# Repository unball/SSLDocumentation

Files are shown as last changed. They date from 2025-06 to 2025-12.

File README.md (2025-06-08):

# SSLDocumentation
Documentação do SSL (Small Size League) da Equipe UnBall

## Indice

- [Fundamentação Teórica](./FundamentacaoTeorica/README.md)
- [Elétrica](./Hardware/Eletrica/README.md)
    - [Componentes](./Hardware/Eletrica/Componentes/README.md)
    - [Movimentação](./Hardware/Eletrica/Projeto-Movimentacao/README.md)
    - [Chute](./Hardware/Eletrica/Projeto-Chute/README.md)
- [Mecânica](./Hardware/Mecanica/README.md)
    - [Base](./Hardware/Mecanica/Base/README.md)
    - [Camisa](./Hardware/Mecanica/Camisa/README.md)
    - [Chute](./Hardware/Mecanica/Chute/README.md)
- [Infraestrutura para testes](./Hardware/Infraestrutura/README.md)
    - [Campo](./Hardware/Infraestrutura/Campo/README.md)
    - [Gol](./Hardware/Infraestrutura/Gol/README.md)
    - [Visão](./Hardware/Infraestrutura/Visao/README.md)
    - [Bancada de Testes](./Hardware/Infraestrutura/BancadaTestes/README.md)
- [Software do Robô](./Software/Robo/README.md)
    - [Firmware](./Software/Robo/Firmware.md)
- [Software da Estratégia](./Software/Estrategia/)
    - [Client](./Software/Estrategia/Client/README.md)
    - [Navegação](./Software/Estrategia/Navegacao/README.md)
    - [Decisão](./Software/Estrategia/Decisao/README.md)

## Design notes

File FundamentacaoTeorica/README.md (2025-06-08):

# Fundamentação Teórica

1. [Design do sistema](Design-sistema.md)
2. [Design do robô](Design-robo.md)
    - [Motor](./Motor/Motor.md)
    - [Acionamento do motor](./Motor/Acionamento-Motor.md)
    - [Rodas](./Rodas/Estudo-tipo-rodas.md)
    - [Cinemática](./Cinematica/Cinematica-robo.md)
    - [Comunicação](./Comunicacao/Comunicacao.md)

## A incluir:
- Sistema de chute

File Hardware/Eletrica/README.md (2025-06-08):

# Sistema elétrico

## Protótipo movimentação

O protótipo será feito por fabricação manual de PCBs em placa de cobre

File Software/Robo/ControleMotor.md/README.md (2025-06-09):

# Controle do motor

## Primeiro passo: controle do torque

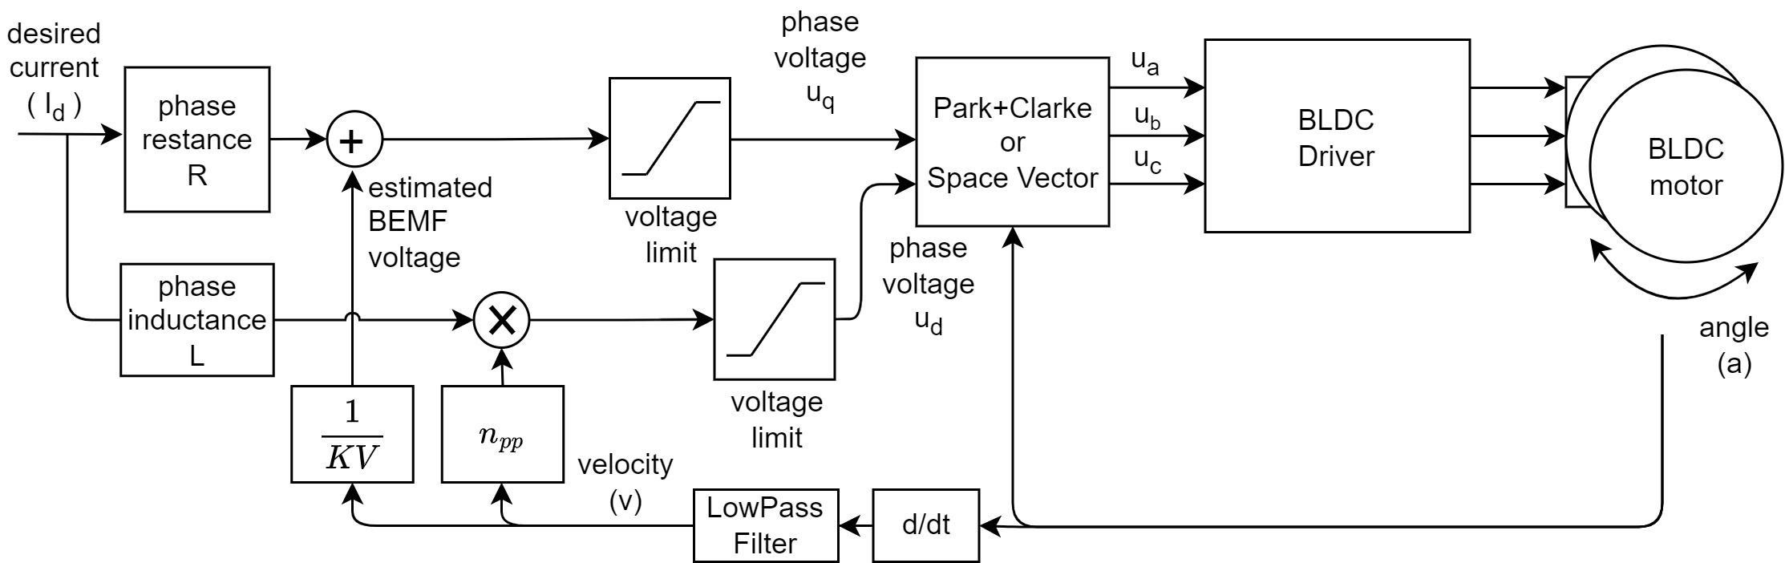
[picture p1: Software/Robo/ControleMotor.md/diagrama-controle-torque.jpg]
Controle-Torque

https://docs.simplefoc.com/voltage_torque_mode
Precisa encontrar os seguintes valores: https://docs.simplefoc.com/bldcmotor

- numero de polos do motor

- indutância L

- KV

- phase resistance 

https://github.com/makerbase-motor/MKS-ESP32FOC/blob/MKS-ESP32-FOC-V1.0/Test%20Code/7_current_control_example/7_current_control_example.ino

https://docs.arduino.cc/software/ide-v2/tutorials/ide-v2-serial-plotter/

https://docs.simplefoc.com/code

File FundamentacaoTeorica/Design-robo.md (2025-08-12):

# Design do robô

## Limitações no design advindas das regras do SSL

### Tamanho 

- O robô deve caber dentro de um cilindro com 0.18m de largura e 0.15m de altura 

### Cores do casco 

- As cores devem ser as mesmas para todos os robôs sendo em um esquema de cor clara e cor escura 
- A cor deve cobrir ao menos 6cm da altura máxima do robô 
- O casco não pode ser refletivo para não interferir na visão 
- As cores não podem ser próximas das cores usadas nos padrões da visão e bola 
- As cores não podem sair durante os jogos 

### Ações do robô 

- O robô deve se movimentar no campo, respondendo aos eventos 
- Para participarmos de competições mundiais, o robô deve chutar a bola 

## Design robô SSL - UnBall

Para facilitar o desenvolvimento do robô, foram definidas etapas para elaborar cada ação que o robô deve fazer no campo quando receber as ações da Estratégia:

### Sistema de Movimentação do Robô

Diz respeito a como o robô vai se movimentar no campo. Para isso, precisamos definir:

- Qual motor usar e como acionar com velocidade desejada?
    - [Estudo do motor](./Motor/Motor.md)
    - [Estudo de como acionar o motor](./Motor/Acionamento-Motor.md)
- Qual roda usar?
    - [Estudo de rodas para robôs omnidirecionais](./Rodas/Estudo-tipo-rodas.md)
- Como transformar a velocidade das rodas na velocidade do robô?
    - [Levantamento da cinemática do robô](./Cinematica/Cinematica-robo.md)
- Como o robô vai saber o que deve fazer?
    - [Comunicação do robô com a Estratégia](./Comunicacao/Comunicacao.md)

### Sistema de Chute

<!-- TODO: incluir links para o sistema de chute -->
Diz respeito a funcionalidade do robô de poder "chutar" a bola. Para isso, precisamos definir:

- Mecânica
- Sistema elétrico
- Quando o chute vai atuar?

## Referência

Buscamos responder as seguintes perguntas do livro _Introduction to autonomous robots_: 

- Como ele se move?
    > R.: Ele pode ir para todas as direções.

- Onde o robô irá se locomover?
    > R.: Em um carpete que será posicionado em cima de uma superfície plana. As dimensões do carpete segue as regras da categoria SSL 

- Como a velocidade das rodas afeta sua posição e velocidade no mundo?  
    > R.: Aqui definimos a cinemática do robô. Isso é detalhado no arquivo [Cinemática](./Cinematica/Cinematica-robo.md)

- Como podemos controlar a velocidade das rodas para atingir uma determinada posição? 
    > R.: Aqui definimos a forma como vai funcionar a Navegação do Robô. Isso é feito na Estratégia. Os detalhes da Estratégia como qual método de navegação vamos usar e qual sistema de decisão vamos aplicar pode ser visto em [Navegação](./Estrategia/Navegacao.md) e [Decisão](./Estrategia/Decisao.md), respectivamente.

- Quais sensores o robô usará pra perceber seu próprio estado no mundo? 
    > R.: As câmeras posicionadas acima do campo dirão sua posição. O giroscópio mede sua orientação em relação ao proprio eixo e o sensor infravermelho irá confirmar se a bola está perto do robô ou não 

- Como extrair informações de seus sensores?
    > R.: Através do Sistema de Visão Computacional Unificado gerido pela organização da categoria SSL. 

- Como o erro da sua percepção no mundo pode ser representado e como lidar diante de situações incertas? 
    > R.: Isso vai ser detalhado em [Navegação](./Estrategia/Navegacao.md) e [Decisão](./Estrategia/Decisao.md).

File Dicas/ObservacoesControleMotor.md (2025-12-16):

# Comentários a respeito do projeto do Controle do Motor GM4108120T com MKS ESP32 DUAL FOC V1.0

## Sobre o driver

### Desvantagens

Não consegue lidar bem com pico de corrente.

Não suporta execução sem limite de corrente.

Sensor de corrente é horrível.

Esp32 ser embutida só trouxe prejuízo. Fica muito dificil de corrigir em hardware os problemas com o sensor de corrente.

Não consegue lidar bem aplicando carga no motor.

Não consegue lidar bem com mau contato no encoder. 

O fusível de proteção queima porém outro componente também queima junto. Não parecia proteger nada.

## Sobre o motor

### Vantagens

É uma opção mais barata que até onde foi usada, se mostrou suficiente.

### Desvantagens

Fabricante chinesa não fornece todas as especificações importantes pro controle do motor. Muitos parâmetros foram assumidos.

O motor sem encoder, vem sem o ímã direcional no eixo.

## Sobre SimpleFOC

### Vantagens

A abstração do FOC em código realmente ajudou a entender melhor como controlar o motor BLDC. 
Seguindo a documentação, é fácil de configurar para usar com o MKS ESP32 DUAL FOC V1.0

### Desvantagens

O uso de tecnicas pra melhorar o controle pode ficar bem engessado pela biblioteca. Se quiser incluir um filtro passa-baixas ou implementar outro controlador, tem que mexer no código fonte da biblioteca

A biblioteca assume que a frequência do loop() do microcontrolador é suficiente pra considerar a discretização do controle como algo contínuo e dá pra sentir como assumir isso deu problemas na prática. Se fosse outra aplicação, menos focada na velocidade do motor, talvez assumir isso não tenha tanto impacto.

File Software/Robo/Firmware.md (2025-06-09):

# Firmware

Arquitetura 

Legenda 

Sistema Central 

Onde fica a inteligência do robô. Vai receber a velocidade (em rad/s ou rpm, depende do que o controle decidir) que o robô deve ter naquele momento e repassar a velocidade para os motores. Também vai receber quando o robô deve fazer o chute 

Comunicação entre microcontroladores 

A comunicação é feita por fio, utilizando o protocolo I2C 

Sistema Periférico 

Não é a parte inteligente mas realiza os cálculos necessários para transformar a velocidade recebida do computador em tensão para as fases do motor. Como o motor é BLDC, precisa de um algoritmo de controle de rotação mais complexo que apenas mandar a tensão para o motor. Para que a rotação seja mais precisa, utilizamos a leitura do encoder que está no motor. 

Comunicação entre driver e motores 

É apenas um fio que envia a tensão de cada fase do motor para que ele gire corretamente 

Motores 

São os motores BDLC. Neles estão acoplados os encoders, que enviam a leitura da posição angular do motor para o Periférico 

Encoders 

São os fios de alimentação do encoder e também de transferência dos dados lidos para o Periférico 

Comentários: 

No diagrama é possível ver que há dois sistemas: 1) Central e 2) Periférico.  

No Sistema Central, temos uma ESP32 WROOM.  
 
No Sistema Periférico, também usamos ESP32 WROOM embutidas no driver MKS DUAL FOC v2.0.  

Cada driver comporta uma ESP e dois motores. Assim é possível executar o FOC o mais rápido possível sem que seus custos computacionais prejudique o acionamento do motor. Pelo menos essa é a ideia inicial.  

Implementação 

Arduíno & C++ 

Organização do código 

https://github.com/unball/FirmwarePerifericoSSL  

https://github.com/unball/FirmwareCentralSSL  

## Comunicação

PC -> roteador -> firmware central -> firmware periferico 

# Visão

# Estratégia

https://github.com/makerbase-motor/MKS-ESP32FOC/blob/MKS-ESP32-FOC-V2.0/Test%20Code/Read%20Before%20You%20Begin.txt 
    ② The open-loop control mode is a test routine, and the heating of the motor is inevitable. Be careful not to get burned!
Please do not run the open-loop routine for more than one minute, otherwise it will cause overheating and burn the motor or circuit board!

https://randomnerdtutorials.com/esp32-spi-communication-arduino/#multiple-devices-same-bus

https://www.quora.com/How-do-I-exchange-data-between-Arduino-and-ESP32-using-serial-communication

https://randomnerdtutorials.com/esp-now-two-way-communication-esp32/

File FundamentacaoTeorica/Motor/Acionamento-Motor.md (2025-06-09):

# Acionamento do motor

## Motor BDLC

### FOC

- [What is FOC? (Field Oriented Control) And why you should use it! || BLDC Motor](https://www.youtube.com/watch?v=Nhy6g9wGHow)
- [Field-Oriented Control](https://www.youtube.com/watch?v=_6-_jvZe7iA)
- [Field-Oriented Control - MathWorks](https://www.mathworks.com/discovery/field-oriented-control.html)

## Controle da velocidade do motor

- FOC
    - Precisa saber a posição do rotor
    - Precisa também monitorar a corrente para não ter perda de energia

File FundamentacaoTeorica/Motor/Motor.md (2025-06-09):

# Motor

## Como motor BDLC funciona

Explicações em Inglês:

- [Playlist Understanding Motors](https://www.youtube.com/watch?v=EHYEQM1sA3o&list=PLaBr_WzeIAixidGwqfcrQlwKZX4RZ2E7D&index=1)
> Explica conceitos mais básicos de eletromagnetismo até como motor BLDC funciona e alguns conceitos importantes para entender FOC

- [Brushless Motor - How they work BLDC ESC PWM](https://www.youtube.com/watch?v=yiD5nCfmbV0)
> Possui animações muito boas para entender como funciona a comutação em um motor BLDC

### Mais referências

- Explicação de como motores elétricos funcionam, com animações: [Playlist de The Engineering Mindset](https://www.youtube.com/watch?v=yiD5nCfmbV0&list=PLWv9VM947MKh3sZh5rjYxrrNno1Mc6cuu)

- Vídeos do MATLAB:
    - [https://www.youtube.com/watch?v=gNpoTPzEkco&t=81s](https://www.youtube.com/watch?v=gNpoTPzEkco&t=81s) 
    - [Understanding Six-step Commutation for BLDC motors| Brushless Motor Control with Simulink, Part 2](https://www.youtube.com/watch?v=WYJWdMV3YMs&t=1s)
    - [BLDC Speed Control Using Pulse Width Modulation (PWM)| Brushless Motor Control with Simulink, Part 3](https://www.youtube.com/watch?v=b5J5qkR7msc)
    - [Understanding Field-Oriented Control | Motor Control, Part 4](https://www.youtube.com/watch?v=YPD1_rcXBIE)
    - [Understanding Space Vector Modulation| Brushless Motor Control with Simulink, Part 5](https://www.youtube.com/watch?v=Gj7qAlsq_m8)
    - [10 Practical Considerations for Implementing Field-Oriented Control (FOC) | Brushless Motor Control](https://www.youtube.com/watch?v=ilN-DauXVFM)

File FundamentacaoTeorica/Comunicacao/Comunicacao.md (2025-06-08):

# Comunicação

## Wireless

### Quais opções temos? Por que vamos usar WiFi?

### WiFi

## Serial

### I2C

### SPI

### PWM

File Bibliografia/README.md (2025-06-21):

# Referências bibliográficas

## Robocup Small Size League Soccer

- [Rules](https://ssl.robocup.org/rules/)
- [Team description papers - TDP](https://ssl.robocup.org/team-description-papers/)
    > "The Team Description Papers (TDPs) and especially the Extended Team Description Papers (ETDPs) are a key element of research and advancement in the Small Size League. Every team is required to submit a TDP or ETDP when qualifying for the RoboCup, describing new concepts and ideas as well as valuable learning experiences."
    >
    > "To search through all TDPs, you can use the [RoboTeam Twente TDP Search Engine](https://tdpsearch.com/)"
- [Open source contributions](https://ssl.robocup.org/open-source-contributions/)
- [Technical Overview of the Small Size League](https://ssl.robocup.org/technical-overview-of-the-small-size-league/#ssl-components):

    SSL Components

## Modern Robotics - Online Course 

- [Playlist no Youtube](https://www.youtube.com/playlist?list=PLggLP4f-rq02vX0OQQ5vrCxbJrzamYDfx)
- [Página principal sobre os cursos online](https://hades.mech.northwestern.edu/index.php/Modern_Robotics#Online_Courses)
- [Códigos no Github](https://github.com/NxRLab/ModernRobotics)

## Documentação ROS 2

- [Cinemática de robôs móveis](https://control.ros.org/humble/doc/ros2_controllers/doc/mobile_robot_kinematics.html)

## Cinemática de robô movél

- [Omnidirectional Control - Raul Rojas](./artigos/omnidrive.pdf)
    > Encontrado na wiki do [RoboTeam Twente](https://wiki.roboteamtwente.nl/technical/control/start)

# Pontos interessantes de outros times 

> Foram escolhidos alguns pontos dos projetos open source de outros times como inspiração para nosso projeto 

## TIGERs-Mannheim

### Base do robô
- https://github.com/TIGERs-Mannheim/mechanics/blob/master/v2020/PDF/01_Grundplatte.pdf
- https://github.com/TIGERs-Mannheim/mechanics/blob/master/v2020/PDF/02_Mittelplatte.pdf
- https://github.com/TIGERs-Mannheim/mechanics/blob/master/v2020/PDF/03_Oberplatte.pdf 

### Chute
- https://github.com/TIGERs-Mannheim/mechanics/blob/master/v2020/PDF/30_Kicker%20Eisen.pdf
- https://github.com/TIGERs-Mannheim/mechanics/blob/master/v2020/PDF/31_Kicker%20Sichel.pdf
- https://github.com/TIGERs-Mannheim/mechanics/blob/master/v2020/PDF/32_Kicker%20Chip.pdf 

### Camisa

- https://github.com/TIGERs-Mannheim/mechanics/blob/master/v2020/STL/Robot/Geh%C3%A4use%20Unterplatte.stl 
- https://github.com/TIGERs-Mannheim/mechanics/blob/master/v2020/STL/Robot/Geh%C3%A4use%20Mantel.stl 

## RobotTeamTwente

### Mecânica
- https://github.com/RoboTeamTwente/mechanics/tree/main/v2024/STL 
- https://github.com/RoboTeamTwente/mechanics/tree/main/v2024/PDF

## RobotJackets

### Firmware
- https://github.com/RoboJackets/robocup-firmware/tree/master/doc 

- kicker -> https://github.com/RoboJackets/robocup-firmware/blob/master/doc/Kicker.md e aqui tbm:  https://github.com/RoboJackets/robocup-firmware/blob/master/doc/Firmware.md

## ZJUNlict

### Mecânica

- https://github.com/ZJUNlict/Mechanics

## Imortals

### Mecânica

- https://github.com/Ma-Ghasemieh/Immortals_ssl_opensource_mech

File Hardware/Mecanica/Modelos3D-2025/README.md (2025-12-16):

# Modelos 

Peças desenvolvidas para o protótipo em dezembro/2025

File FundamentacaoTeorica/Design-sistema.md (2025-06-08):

# Design do sistema 

<!-- TODO: incluir link para o material das equipes  -->
O sistema é desenvolvido seguindo as regras da categoria [Robocup Small Size League](https://robocup-ssl.github.io/ssl-rules/sslrules.pdf ). Além do que foi feito por outras equipes que participam da categoria há mais tempo tais como Tigers, Robocin, ITA, entre outras.

Diante desse cenário, temos que o sistema pode ser representado da seguinte forma:

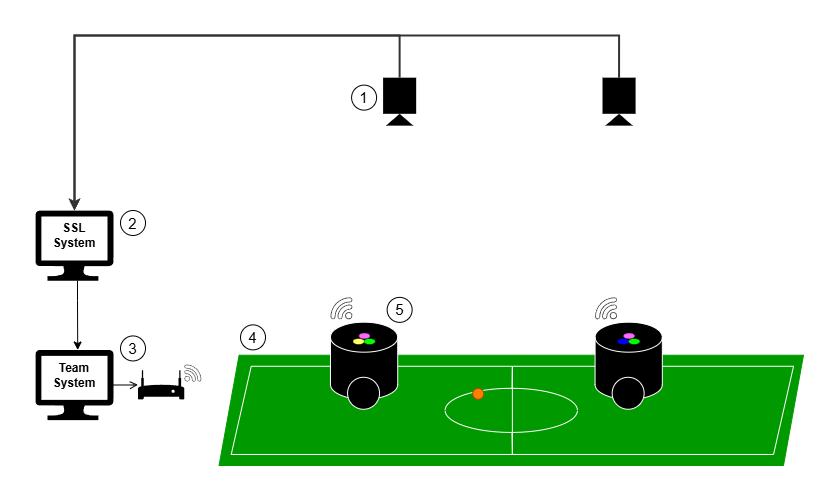
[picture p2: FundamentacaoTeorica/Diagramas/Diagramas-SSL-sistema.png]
Desenho simplificado do sistema do Small Size League


O sistema conta com:

<!-- TODO: incluir quais cameras sao geralmente usadas -->
1 - Sistema de Visão

- Duas câmeras posicionadas acima do campo
- Software de visão computacional unificado, que processa as informações lidas pelas câmeras e envia para os Sistemas de Software das equipes

<!-- TODO: incluir referencia para os repositorios do SSL -->
2 - Sistema SSL

- Consiste do Software de Visão Computacional e do Game Controller

<!-- TODO: incluir link para os softwares da equipe -->
3 - Sistema de software da Equipe

- Recebe as informações processadas pelo Sistema de Visão. No caso da Equipe UnBall, ao receber as informações, processa a navegação e decide a ação de cada robô do time naquele momento. A decisão é enviada, então, para cada robô via comunicação wireless. No desenho, essa comunicação se dá por WiFi, mas pode ser de outros tipos desde que atenda às regras da categoria.

4 - Campo

- O campo é feito de carpete e segue as regras definidas pela Robocup. 
- A bola é uma bola de golfe laranja
- Os gols, que não foram desenhados no diagrama acima, devem ser brancos e de dimensões de acordo com as regras da categoria.

5 - Robôs

- Os robôs compõe o time e, de acordo com as regras, possuem restrições em tamanho de 18cm de diâmetro e 15cm de altura. Eles recebem as ações decididas pelo Sistema da Equipe e atuam para tal. Além de se movimentar para o local decidido, eles podem chutar e driblar. Os robôs da UnBall apenas movimentam e chutam com força máxima.

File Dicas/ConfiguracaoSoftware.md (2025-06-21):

# Tutoriais de instalação dos softwares usados no SSL

## Requisitos mínimos para executar os sistemas de software
[A definir]

----

> :information_source: Info :information_source::
>
> Para saber mais sobre os softwares, acessar [Technical Overview of the Small Size League](https://ssl.robocup.org/technical-overview-of-the-small-size-league/)

1. [Tutorial SSL-Vision](https://github.com/unball/tutoriaisunballmd/blob/main/tutorialsslvision.md)

2. [Tutorial GrSim](https://github.com/unball/tutoriaisunballmd/blob/main/GrSim.md)

3. [SSL Game Controller](https://github.com/RoboCup-SSL/ssl-game-controller)

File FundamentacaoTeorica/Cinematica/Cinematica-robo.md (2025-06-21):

# Cinemática

<!-- TODO: o que é a cinematica e por que vamos precisar dela?  -->

## Definir configuração das rodas do robô

### Possíveis configurações do robô omnidirecional 
 
Vamos trabalhar com robôs holonomicos: Não tem restrição de movimento. Ele pode ir para qualquer lugar a qualquer instante. Pode ter 3 rodas ou 4 rodas 

#### Configuração do robô com 3 rodas

Três rodas omni montadas em uma configuração triangular com seus eixos inclinado em 120 graus em relação entre si:

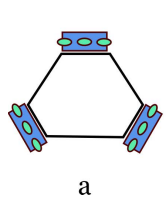
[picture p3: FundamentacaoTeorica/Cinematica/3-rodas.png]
3-rodas


#### Configuração do robô com 4 rodas

Rodas omni simétricas em 90 graus. Configuração '+' em b e 'x' em c:

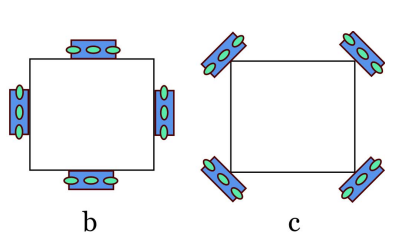
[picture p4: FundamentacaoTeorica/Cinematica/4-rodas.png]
dois tipos de omni com 4 rodas


Rodas mecanum como se fosse um carro:

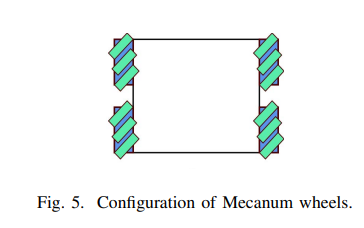
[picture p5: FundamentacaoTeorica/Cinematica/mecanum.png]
carro


#### Comparação entre 3 rodas e 4 rodas em 'x' 
> Referência: Modeling and Assessing of omni-directional robots with three and four wheels 

|  | Número de rodas | Tipo de rodas | Prós pro SSL | Contras pro SSL |
|---|---|---|---|---|
| Omni | 3 | Omni | Cria 3 pontos de contato (um plano) com mesma pressão nas rodas. Precisa de menor corrente pra atingir velocidade máxima que 4 rodas | Aceleração menor que 4 rodas |
| Omni | 4 | Omni | Aceleração bem mais rápida | Consome mais potência. Pode precisar de suspensão pra compensar a roda que fica suspensa e garantir pressão igual nas rodas que ficam no chão |
| "Carro" | 4 | Mecanum |  | Pode não caber bem dentro do cilindro limite da categoria. Qualquer espaço é sagrado |

*Observação:* 

É possível usar rodas mecanum em robôs omni na configuração de 3 rodas e 4 rodas. Porém a roda mecanum pode gerar uma limitação na movimentação do robô que deve ser considerada no projeto do controle do robô. Também não foram encontrados exemplos usando algo assim, então pra ter certeza que funcionaria no SSL teria que fazer algum estudo primeiro.  

### Configuração escolhida e justificativa 

#### Configuração de 4 rodas omnidirecionais

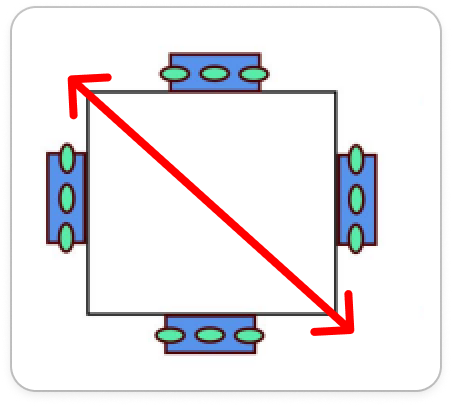
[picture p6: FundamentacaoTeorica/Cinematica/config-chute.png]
4 rodas omni


##### Motivos: 

1. Tem espaço pro sistema de chute, como indicado na figura pela seta vermelha 
2. Permite "esconder" as rodas com a camisa do robô  
3. Aceleração maior com 4 rodas indica que robô vai ser mais rápido para chegar na bola, pra defender a área aliada, etc 

## Formulação matemática

<!-- TODO: incluir formulas da cinematica do robo  -->

> Referência: [Omnidirectional Control](../../Bibliografia/artigos/omnidrive.pdf)

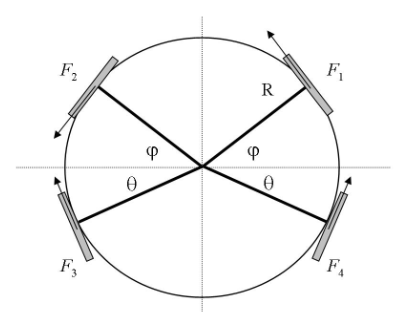
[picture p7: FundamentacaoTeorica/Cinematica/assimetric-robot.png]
Robô assimétrico


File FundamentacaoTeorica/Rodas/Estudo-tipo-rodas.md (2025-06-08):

# Tipos de rodas para robôs omnidirecionais 

## Comparação entre os tipos de rodas: 
> Fonte: A Comparative Review of Omnidirectional Wheel Types for Mobile Robotics 

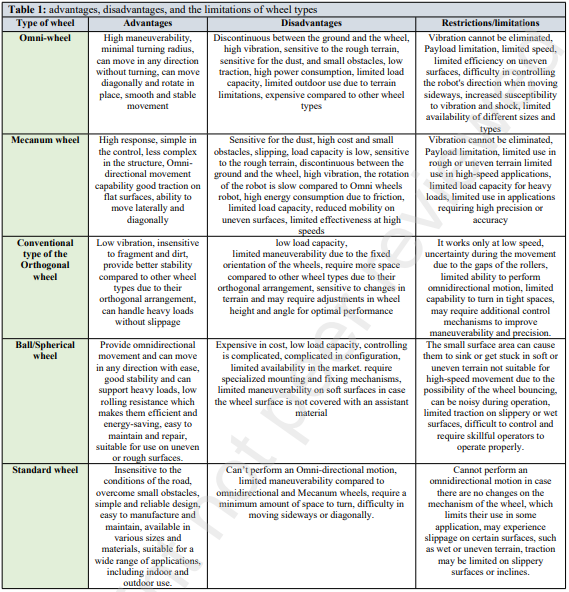
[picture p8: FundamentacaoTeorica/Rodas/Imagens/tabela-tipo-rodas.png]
tabela com tipos de rodas para robôs omnidirecionais

 
### Roda omnidirecional 
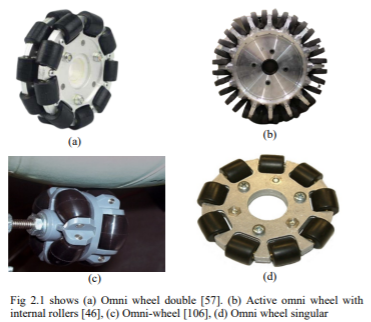
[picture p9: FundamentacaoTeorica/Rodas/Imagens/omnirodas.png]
roda omnidirecional


### Roda mecanum
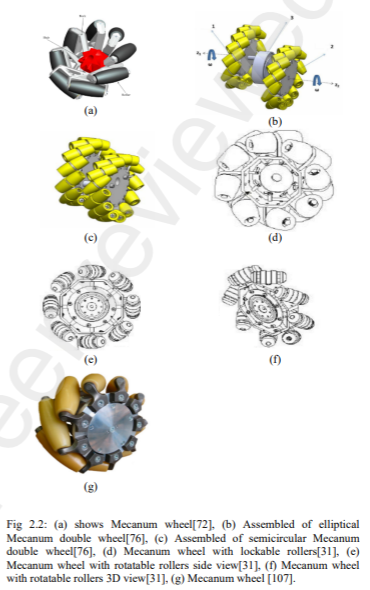
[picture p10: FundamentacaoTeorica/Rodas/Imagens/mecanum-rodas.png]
roda mecanum


### Roda ortogonal 
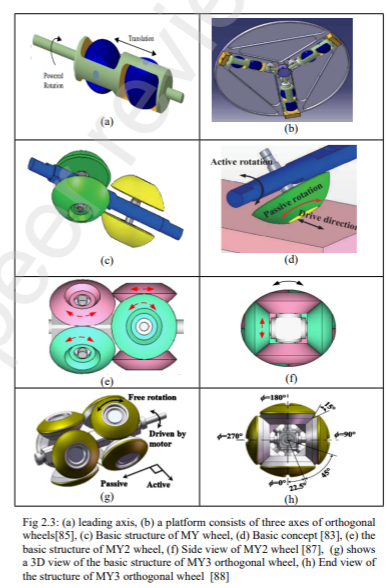
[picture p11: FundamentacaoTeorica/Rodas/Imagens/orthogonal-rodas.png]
roda ortogonal


### Roda esférica  
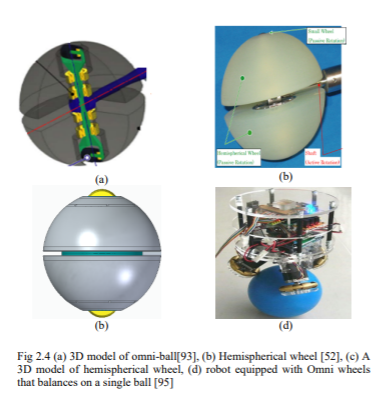
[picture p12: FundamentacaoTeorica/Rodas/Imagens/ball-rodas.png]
roda esferica


### Roda tradicional 
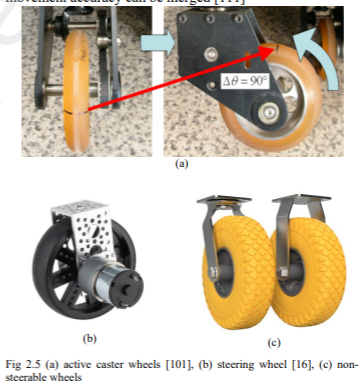
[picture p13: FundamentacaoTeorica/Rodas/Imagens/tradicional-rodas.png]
roda tradicional


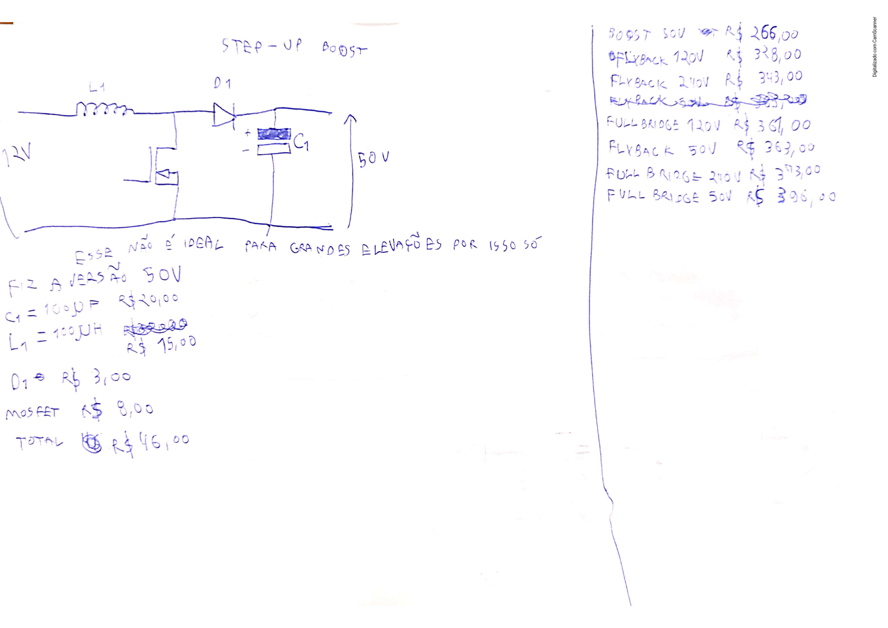
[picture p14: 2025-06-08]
Hardware/Eletrica/Projeto-Chute/Imagens/GetImage (11).png

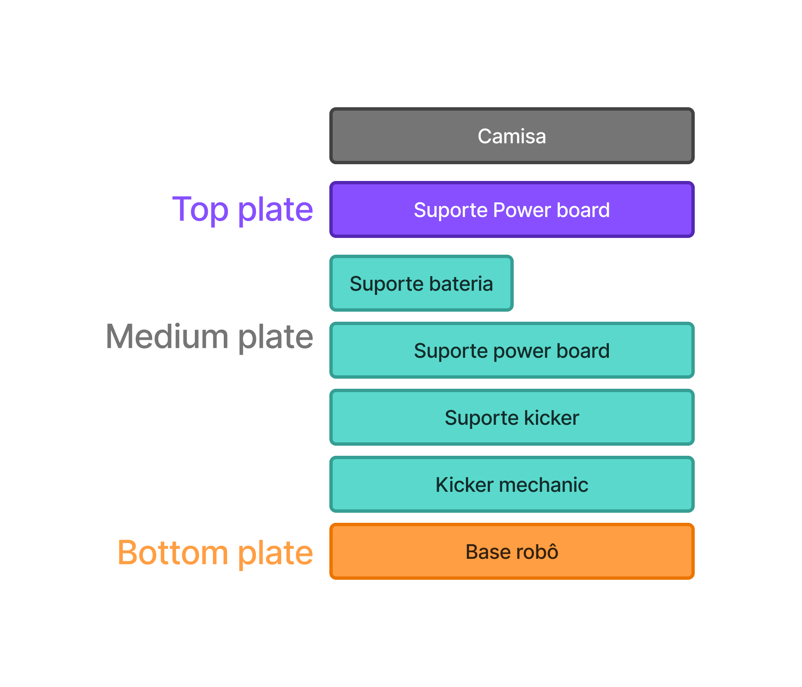
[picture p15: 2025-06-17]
Hardware/Eletrica/esquema-mecanica.png

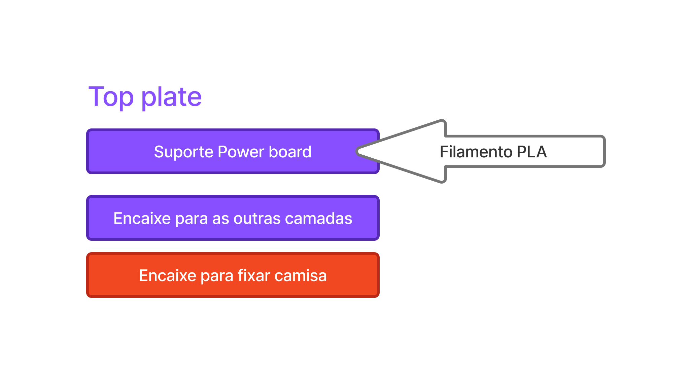
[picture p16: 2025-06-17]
Hardware/Eletrica/esquema-top-plate.png

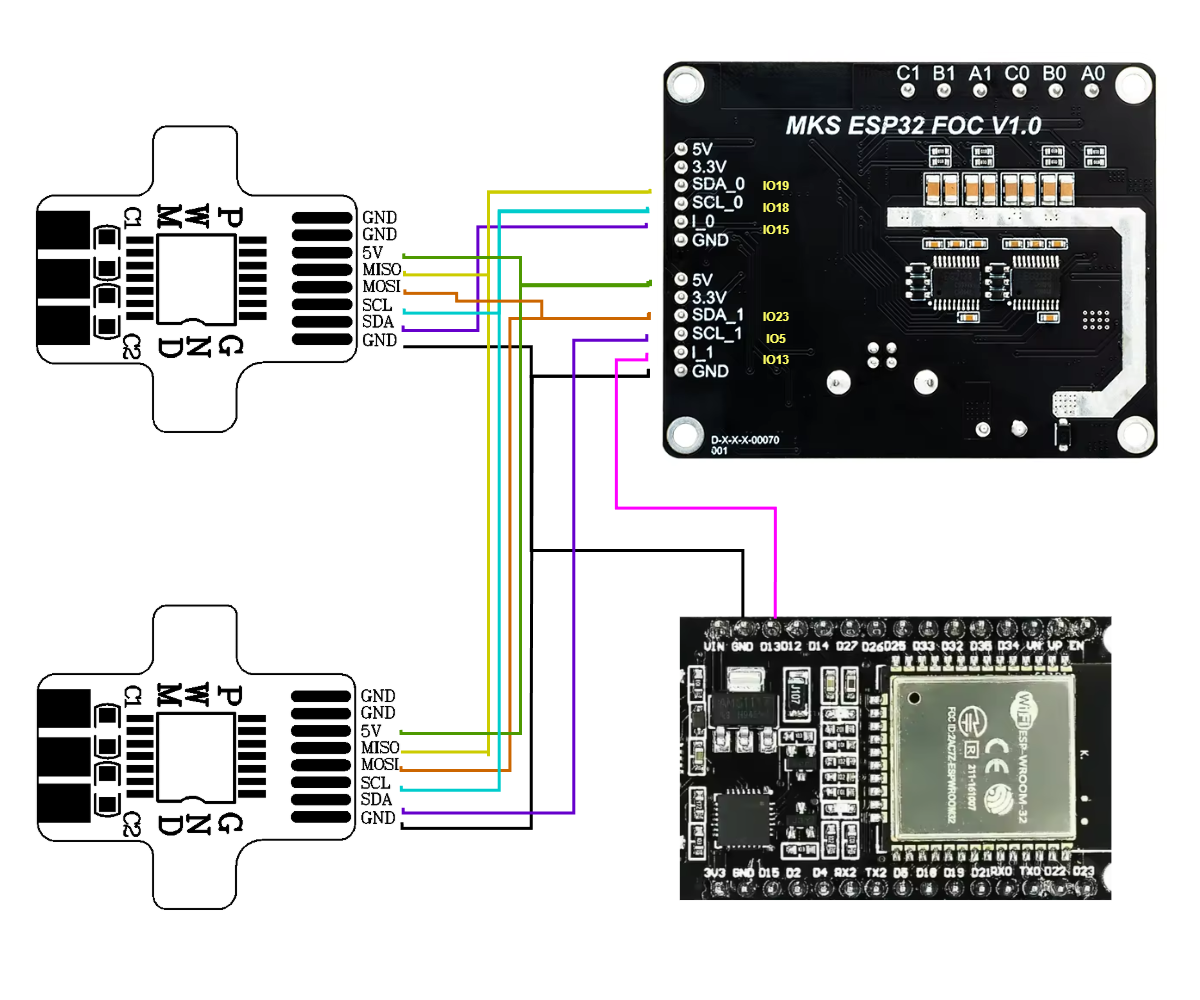
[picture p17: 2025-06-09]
Hardware/Eletrica/Pinout.png

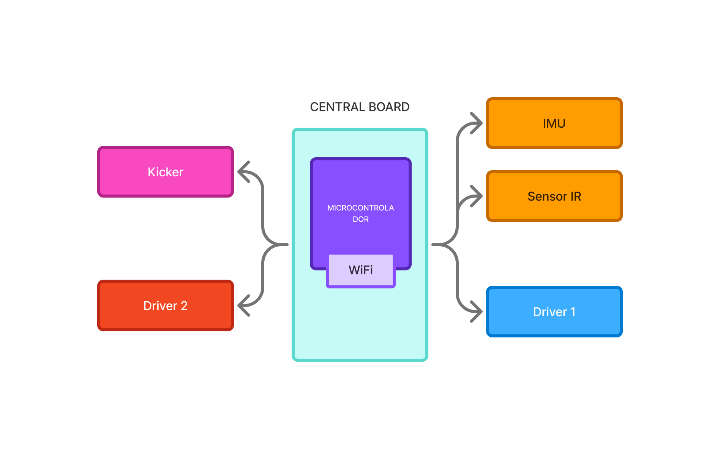
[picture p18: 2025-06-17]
Hardware/Eletrica/arquitetura-central-board.png

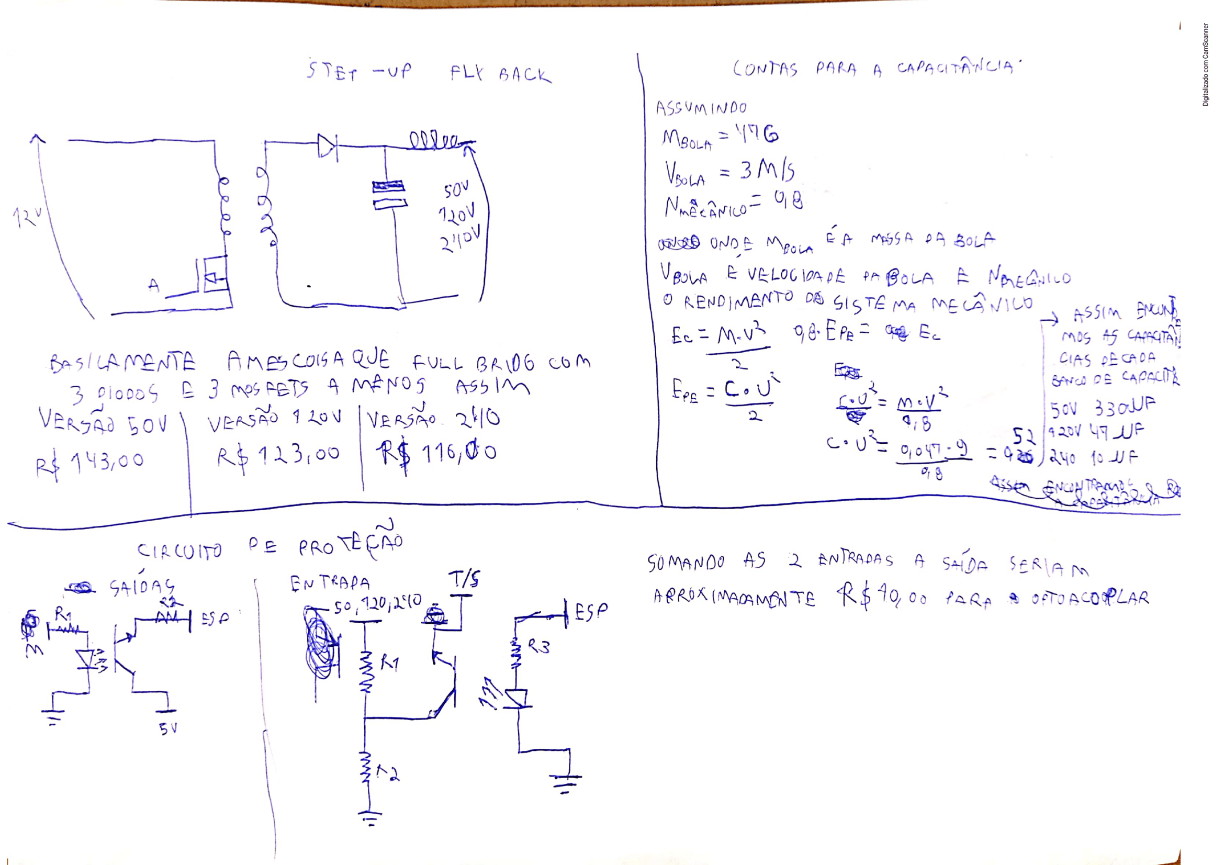
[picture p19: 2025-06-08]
Hardware/Mecanica/Chute/Imagens/GetImage (12).png

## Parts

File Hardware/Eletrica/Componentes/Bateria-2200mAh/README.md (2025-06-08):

2200mAh
3S
30C 
Discharge
11.1V
24.42WH

Alimentação 

Conector XT60
Diâmetro fio: 4mm
12AWG 
200°C

Balanceamento

Conector dupont (acho que é JST na verdade)
12mm×5mm
22AWG
200°C
Diâmetro: 1.6mm

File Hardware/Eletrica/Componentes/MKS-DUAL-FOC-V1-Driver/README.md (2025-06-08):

# MKS DUAL FOC V1.0

Link fabricante: https://makerbase3d.com/product/esp32-foc/?srsltid=AfmBOooP9k1y0BmLpniX1oX0SurjO4H1KHm1H5UuaNR8bcujxwjDCpm2

Codigo de teste:
https://github.com/makerbase-motor/MKS-ESP32FOC/tree/MKS-ESP32-FOC-V1.0 

Manual:
https://github.com/makerbase-motor/MKS-ESP32FOC/tree/MKS-ESP32-FOC-V1.0/User%20Manual

O driver que utilizamos é o MKS DUAL FOC v2.0. Ele foi escolhido por conta da ESP embutida. Existem outras versões do driver da mesma fabricante que podem ser usadas. Até agora, só achei v1.0, v2.0, v3.1/v3.2. A fabricante fornece documentação de cada uma com manual, esquemático e testes de rotina:  

MKS dual FOC v1.0: https://github.com/makerbase-motor/MKS-ESP32FOC/tree/MKS-ESP32-FOC-V1.0  

MKS dual FOC v2.0: https://github.com/makerbase-motor/MKS-ESP32FOC/tree/MKS-ESP32-FOC-V2.0  

MKS dual FOC v3.1/3.2: https://github.com/makerbase-mks/MKS-DUALFOC/tree/main 

Também achei esse repositório com links e documentos que podem ser úteis para gente, juntando datasheet de encoder, driver, código para o driver, etc: https://github.com/makerbase-mks/simplefoc-MKS/tree/main/02_Makerbase%20Simple%20FOC%20related%20documents  e https://github.com/makerbase-mks  
 
O SimpleFOC (https://simplefoc.com/) fornece uma biblioteca que facilita muito a implementação do FOC no arduíno. Como o MKS DUAL FOC v2.0 tem uma ESP32, é possível utilizar arduino também. Por esse motivo de ser mais amigável, sem precisar implementar o FOC do zero, vamos utilizar arduíno nessa arquitetura.

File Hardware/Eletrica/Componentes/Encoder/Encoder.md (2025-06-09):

# Encoder

Link Iflight AS5048A: https://shop.iflight.com/as5048a-magnetic-encoder-pro262 

Foi escolhido outro encoder além do AS5048A. O motivo pra escolher o AS5600 foi por conta de ser mais barato q o outro. Nao foram vistos mais opçoes de encoder de outras fabricantes. Tbm tem exemplos do MKS DUAL FOC v1.0 usando o AS5600

https://community.simplefoc.com/t/b-g431b-esc1-seeed-groove-as5600-reading-problems-in-i2c-and-pwm-modes/4323

https://community.simplefoc.com/t/as5600-angle-sensor-support/42/6

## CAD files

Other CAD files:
Hardware/Infraestrutura/BancadaTestes/suporte-motor/support-motor-v4.f3d
Hardware/Mecanica/Modelos3D-2025/CASE_BATERIA.f3d
Hardware/Mecanica/Modelos3D-2025/ESPAÇADOR_BOT_MID.f3d
Hardware/Mecanica/Modelos3D-2025/ESPAÇADOR_MID_TOP.f3d
Hardware/Mecanica/Modelos3D-2025/arruela_suporte_camadas_6mm_0-8mm.f3d
Hardware/Mecanica/Modelos3D-2025/bot.f3d
Hardware/Mecanica/Modelos3D-2025/mid-2.f3d
Hardware/Mecanica/Modelos3D-2025/suporte_motor_COM_case_encoder.f3d
Hardware/Mecanica/Modelos3D-2025/top2.f3d

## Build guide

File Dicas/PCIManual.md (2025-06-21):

# Placas de circuito impresso

## Eletrônica UnBall

Por questão de custos financeiros, a equipe optou por fabricar suas placas eletrônicas praticamente de forma manual. A fabricação conta com os seguintes materiais:

- Placa de cobre liso
- Circuito impresso a laser em um papel sulfite ou de fotografia
- Percloreto de ferro
- Acetona ou ferro de passar 
- Água corrente
- Agulha para ajustar trilhas
- Caneta permanente

A fabricação pode seguir um dos seguintes tutoriais:

- [Prof. Elias Faustino: Como fazer uma placa de circuito impresso](https://www.youtube.com/watch?v=2Rjfhq5LOv8)
- [Márcio Soares (Arne) Aprenda como fazer placas de circuito impresso com acabamento semiprofissional](https://www.youtube.com/watch?v=LEJJjEaGJ7c)
    > Utiliza impressora a laser; papel sulfite; ferro de passar roupas; ácido;  passa bombril pra retirar o toner; alinha um papel com o desenho dos componentes por baixo alinhado com as trilhas pra saber onde soldar e o q soldar
- [FunBots: COMO FAZER UMA PCB! | Método Simples, Rápido e Barato de PCI Caseira](https://www.youtube.com/watch?v=9YGTZ671VJA)
    > Faz o depósito do toner com acetona e pressão, ajusta trilhas com agulha e caneta permanente. Verifica se não há curto circuito entre as trilhas com um multímetro.
- [FunBots: COMO FAZER UMA PCB DUPLA FACE | PCI Caseira e simples com Acetona](https://www.youtube.com/watch?v=V0aOzRYOyko)

:information_source: É possível fabricar PCIs com solda reflow:

- [FunBots - Como fazer pcb com solda reflow (manualmente)](https://www.youtube.com/watch?v=JNrhAweeBnA&list=PLEkoGrN4bx1C-09VuAwZD36ZT5E8RC5Pc&index=6)

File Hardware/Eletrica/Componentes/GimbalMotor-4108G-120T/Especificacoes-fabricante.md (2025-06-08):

Motor gimbal 4108H da Iflight: https://shop.iflight.com/ipower-motor-gm4108h-120t-gimbal-motor-with-as5048a-encoder-pro243  

Model: GM4108H 

Motor Out Diameter: Ф47±0.05mm 

Configuration: 24N/22P 

Motor Height: 32.3±0.2mm (Included with Encoder housing) 

Hollow Shaft(OD): Ф10-0.008/-0.012mm 

Hollow Shaft(ID): 8+0.05/0mm 

Wire Length: 265±3mm 

Cable AWG: #24 

Motor Weight: 137±0.5g 

Wire plug: 2.5mm dupont connector 

No-load current: 0.07±0.1A 

No-load volts: 20V 

No-load Rpm: 513~567 RPM 

Load current: 1.5A 

Load volts: 20V 

Load torque(g·cm): 1200-1800 

Motor internal resistance: 11.1Ω±5%（Resistance varies with temperature） 

High voltage test: DC500V 1mA@2sec 

Rotor housing runout: ≤0.1mm 

Steering (axle extension): Clockwise 

High-low temperature test： 

High temperature: Keep at 60℃ for 100 hours, and the motor can work normally after 24 hours at room temperature 

Low temperature: Keep at -20℃ for 100 hours, and the motor can work normally after 24 hours at room temperature 

Maximum power: ≤25W 

Working current: 3-5S 

Working temperature: -20~60℃;10~90%RH

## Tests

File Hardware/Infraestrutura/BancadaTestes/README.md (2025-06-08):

## suporte motor
primeira versao do suporte -> [v1.0](./suporte-motor/support-motor-v4.f3d)
- pontos que podem melhorar
    - colocar furos pra motor sem encoder
    - fazer mais alto para caber a roda de 9cm de diametro
    - talvez aumentar a base?

ideia de suporte -> https://community.simplefoc.com/t/ipower-gm4108h-120t-motor-mount-bracket-stl-file/2060/8

## ideias

- suporte driver
- suporte bateria

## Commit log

2025-06-08 add esp32
2025-06-09 lets q bora, um monte de link
2025-06-15 medo de direitos autorais
2025-06-17 um monte de coisa ihaaa
2025-06-21 inclui datasheet regulador de tensao
